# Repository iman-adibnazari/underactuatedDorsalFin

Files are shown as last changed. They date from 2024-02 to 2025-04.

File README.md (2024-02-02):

## Overview
- Proposing an efficient fish robot design where, leveraging the physical properties of the dorsal fin material, only the front part of the fin is motor-driven to initiate wave propagation
- Design a linear quadratic regulator(LQR) and feedforward controller to manage the movement of the fish's fin

## Set up
Install necessary packages listed in requirements.txt:
`$ pip install -r requirements.txt`

## Robot Assembly
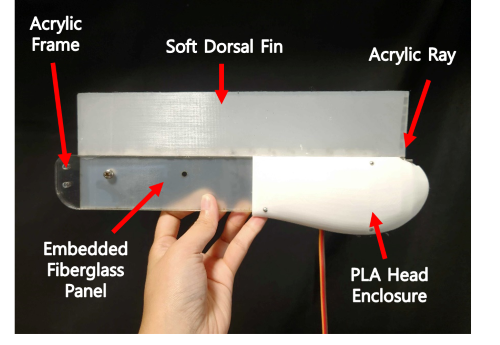
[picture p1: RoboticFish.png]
Schemetic view of robotic fish

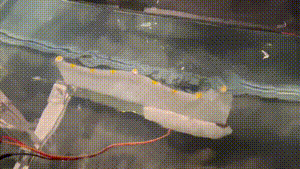
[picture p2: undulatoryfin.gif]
Propulsion of wave through dorsal fin

1. Laser-cut acrylic fin ray, fish body acrylic Frame, Fiberglass Panel
```
cad\Fish\FinRay.SLDPRT
cad\Fish\Body2.SLDPRT
cad\Fish\FIN.SLDPRT
```
2. Build silicone fin using 3D printed mold embedded with FR4 and fin ray 
```
cad\Fin Silicone Mold\Fin_mold_assemble.SLDASM
```
3. 3D printing PLA Head Closure 
```
cad\Fish\Body1_L.SLDPRT
cad\Fish\Body1_R.SLDPRT
```
4. Assemble 
- Mount dowel pin, Savox SW0250MGP motor with left Head Closure
- Attach fin with acrylic body frame
- Combine left head closure and acrylic body frame with fin 

## Control System Modeling
Goal: Aim to control the wave motion of the undulatory dorsal fin of robotic fish
Approach: Employing a frequency-response-based control system modeling method
1. Use top-view video data of the fish's fin, run `src\dataGenProc\multiObjectTracking.py` to calculate each position of the fin over time
2. Run `src\dataGenProc\GenerateBodedata.py` to create Bode plot using the processed video data
3. Run `src\dataGenProc\EstimateTF.m` in MATLAB to estimate Transfer Function from Bode plot, and generate discrete time state-space model
4. Design LQR gain, Kalman filter gain by running `src\dataGenProc\ControllerDesign.m` in MATLAB

## Testing Controller in Robotic Fish
1. Run `src\controlSystem\realTimeTracking.py` to track the tail point of the fin and send it to Arduino
2. Execute `src\controlSystem\discretecontroller\discretecontroller.ino` in Arduino IDE to output motor sine wave frequency

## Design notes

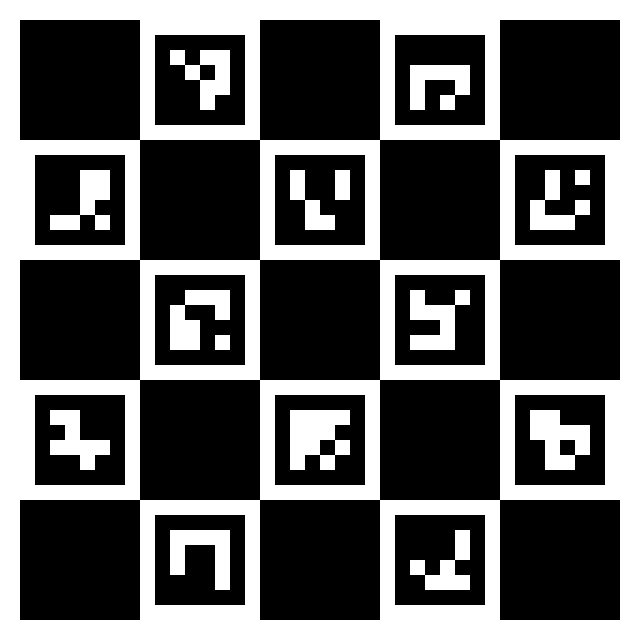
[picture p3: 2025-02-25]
src/python/utils/ChArUco_Marker.png

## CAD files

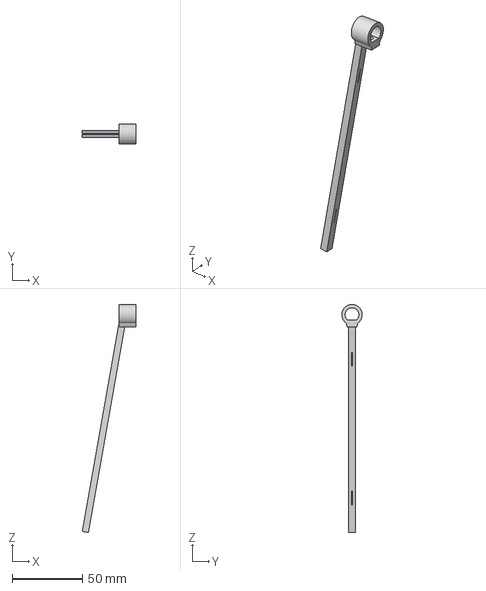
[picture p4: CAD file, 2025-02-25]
cad/CNC/FinRayv184.step
38.0 x 14.5 x 162.1 mm

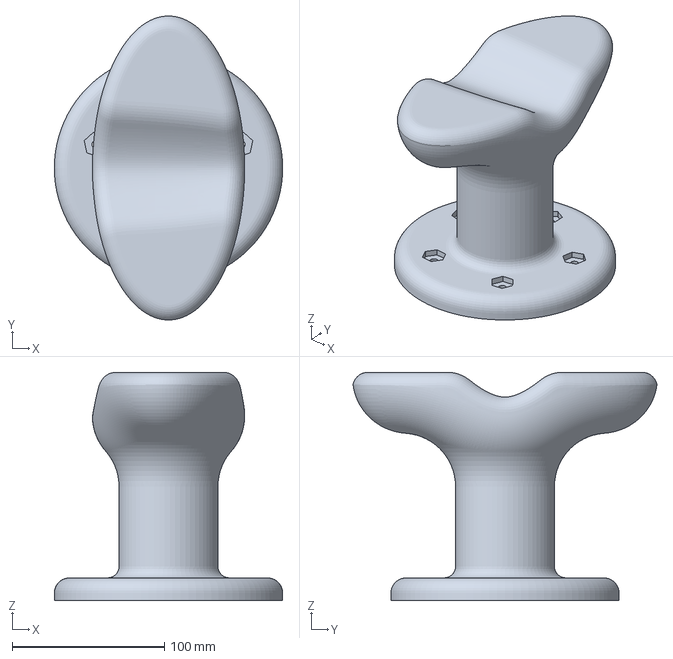
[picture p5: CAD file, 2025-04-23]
cad/fabrication/Bambu/StandPillarRight.3mf
150.0 x 199.6 x 150.0 mm

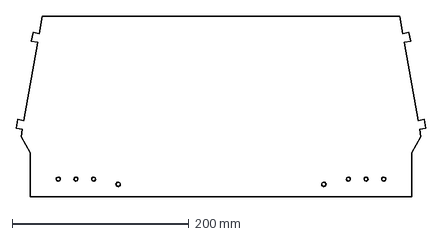
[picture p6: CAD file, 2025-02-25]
cad/fabrication/dxf/Fin_TPU.dxf
463.8 x 204.4 mm

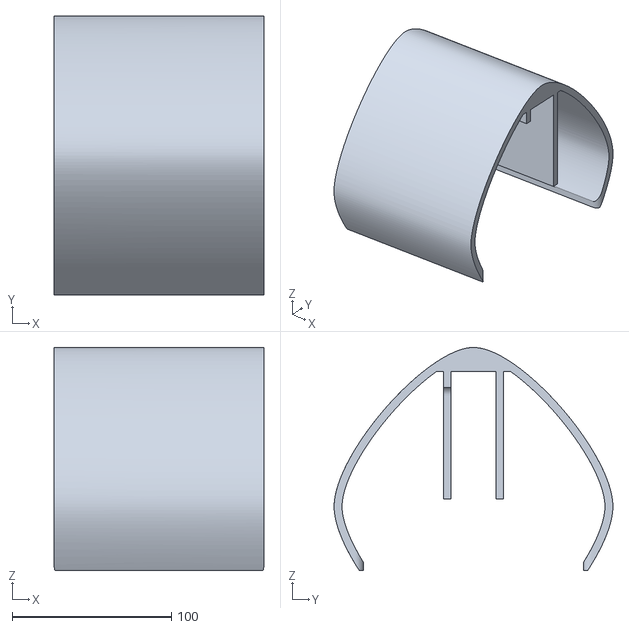
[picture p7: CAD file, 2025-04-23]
cad/fabrication/stl/FrameCover_ExternalFrame_v217.stl
131.8 x 175.0 x 140.0

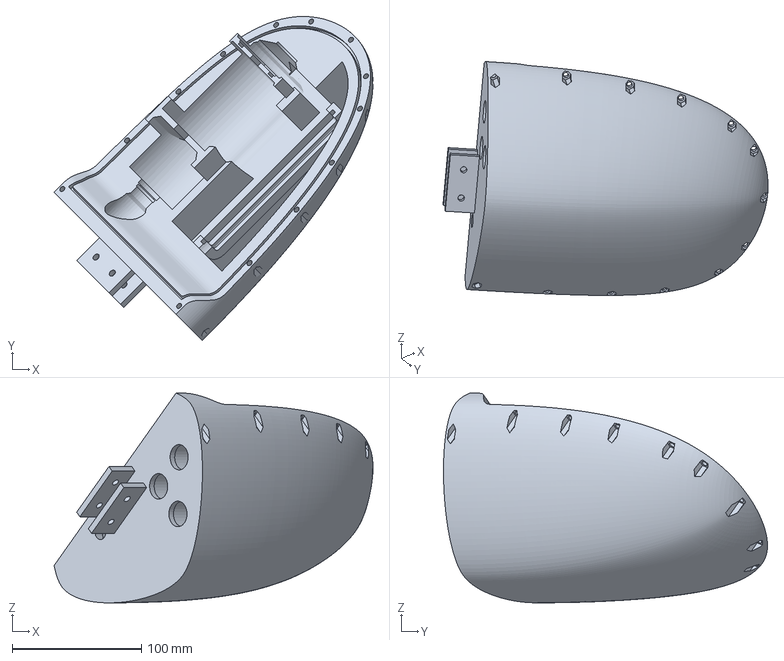
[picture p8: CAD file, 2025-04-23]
cad/fabrication/Bambu/HeadBottom.3mf
246.9 x 250.9 x 162.4 mm

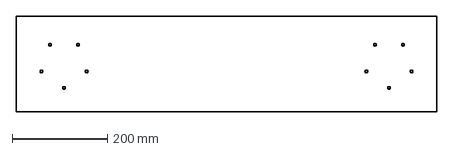
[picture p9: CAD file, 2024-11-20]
cad/fabrication/dxf/StandBase_Acrylic.dxf
882.0 x 200.0 mm

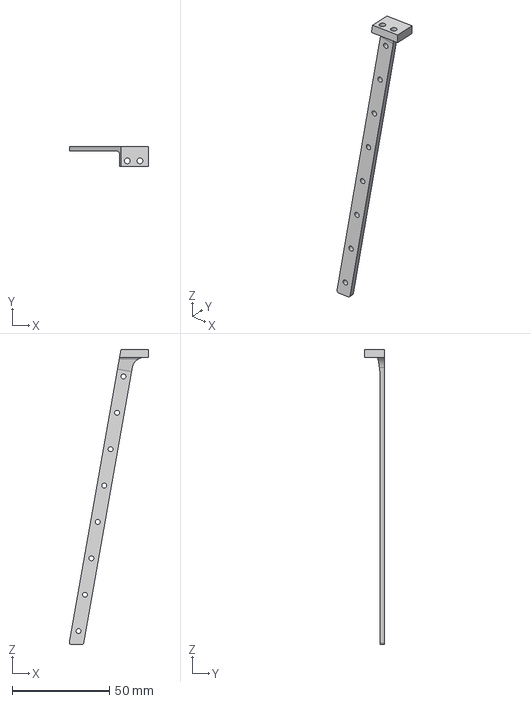
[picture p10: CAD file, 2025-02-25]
cad/fabrication/stepFiles/Finray_v212_Side1.step
40.9 x 10.5 x 151.7 mm

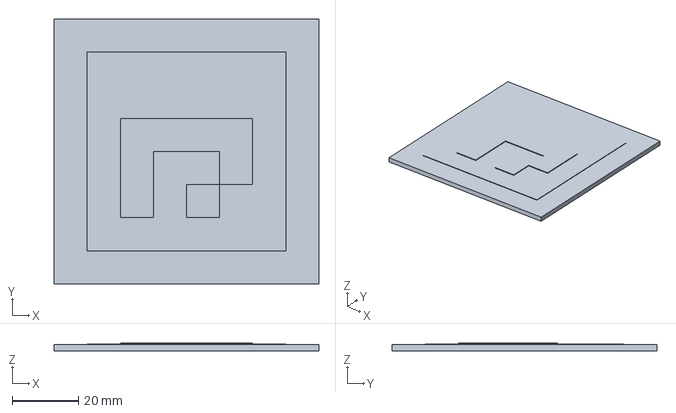
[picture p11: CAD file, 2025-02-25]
cad/fabrication/stl/ArUco_4x4_50_ID1.3mf
80.0 x 80.0 x 2.50 mm

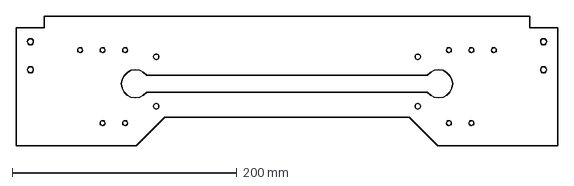
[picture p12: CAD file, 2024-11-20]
cad/fabrication/dxf/BodyFrame_Acrylic.dxf
482.0 x 115.0 mm

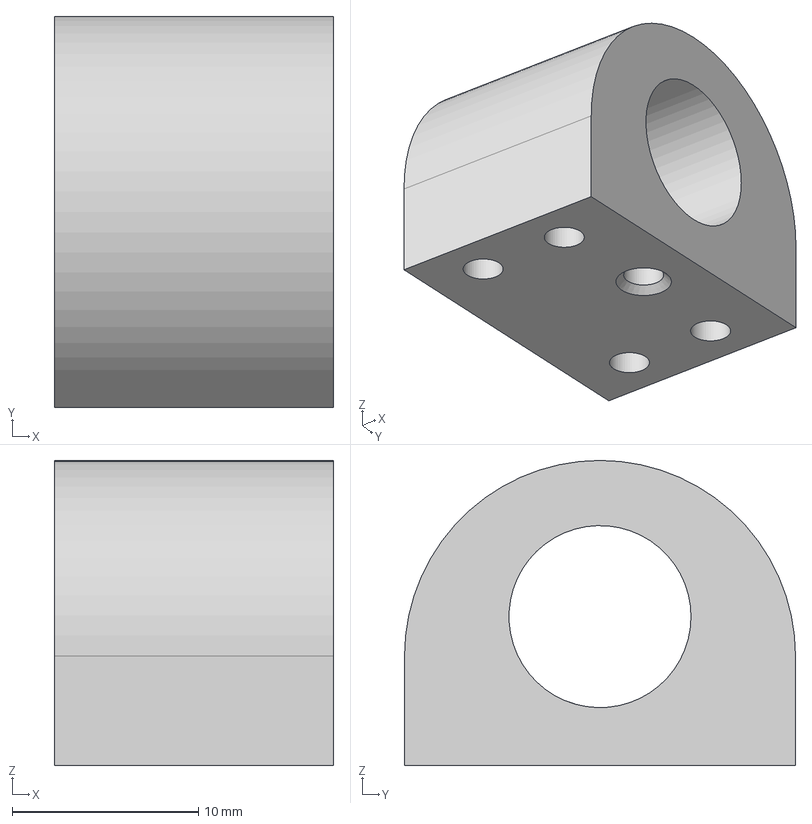
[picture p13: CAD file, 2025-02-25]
cad/fabrication/stepFiles/Finray_v212_ShaftCouple.step
15.0 x 21.0 x 16.4 mm

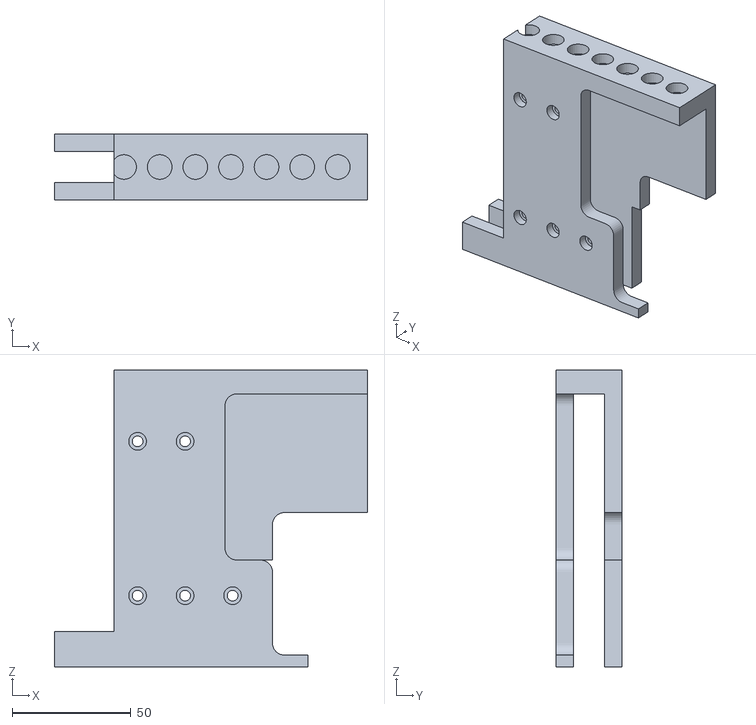
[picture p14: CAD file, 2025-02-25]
cad/fabrication/stl/FrameCover_FrameMount.stl
131.8 x 27.9 x 125.0

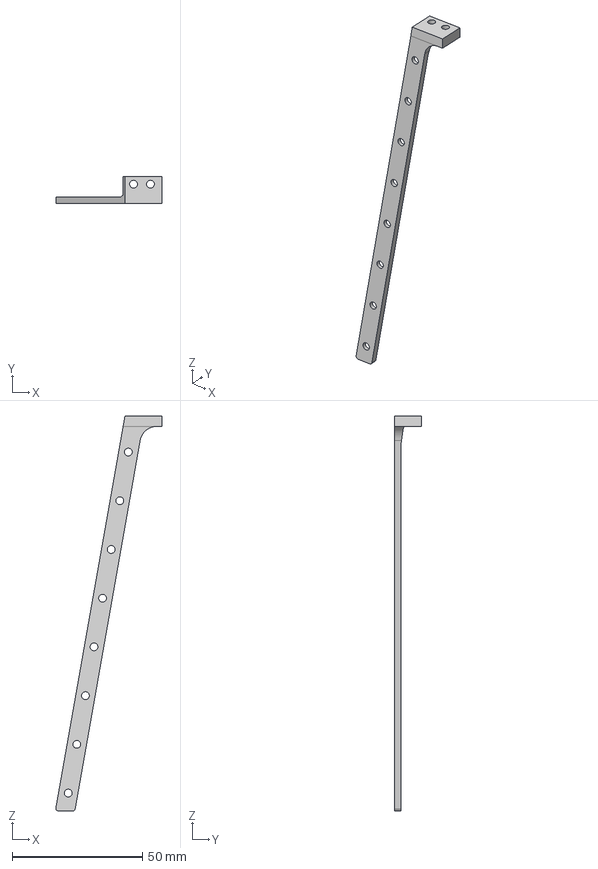
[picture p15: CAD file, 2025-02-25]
cad/fabrication/stepFiles/Finray_v212_Side2.step
40.9 x 10.5 x 151.7 mm

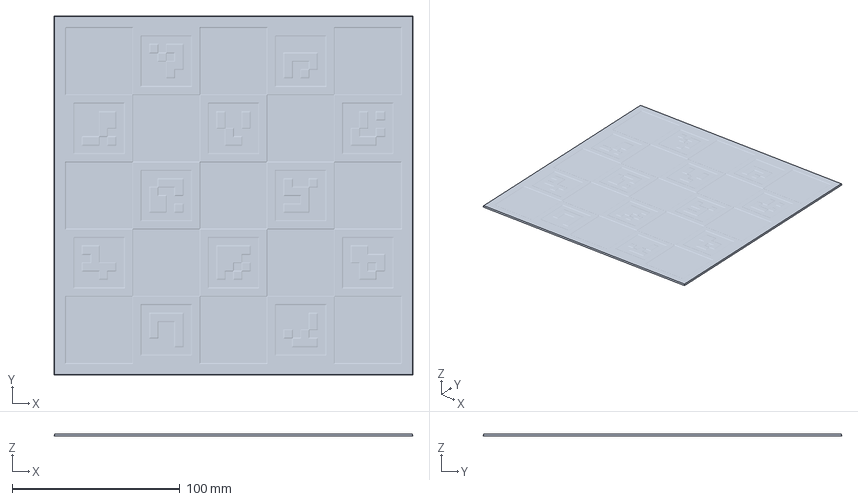
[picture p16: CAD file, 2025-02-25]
cad/fabrication/Bambu/ChArUco_Board_4x4_100_40mmSquares.3mf
213.8 x 213.8 x 1.20 mm

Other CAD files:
cad/fabrication/stepFiles/finRayV193.step
cad/fabrication/Bambu/StandPillars.3mf
cad/fabrication/Bambu/FrameCovers_FrameCoverOnly.3mf
cad/fabrication/stl/FinRay.stl
cad/fabrication/stl/ArUco_4x4_50_ID0.stl
cad/fabrication/Bambu/ArUco_4x4_50_ID0.3mf
cad/fabrication/Bambu/BatteryModule-Covers.3mf
cad/fabrication/Bambu/BatteryModule-ModuleBody.3mf
cad/fabrication/Bambu/BatteryModule-PowerDistBoardHolder.3mf
cad/fabrication/Bambu/ElectronicsBasePlate.3mf
cad/fabrication/Bambu/FinRay.3mf
cad/fabrication/Bambu/FrameCover.3mf
cad/fabrication/Bambu/FrameCovers_FrameMountsOnly.3mf
cad/fabrication/Bambu/HeadTop.3mf
cad/fabrication/Bambu/PowerDistBoardHolder.3mf
cad/fabrication/stepFiles/finRayV190.step
cad/fabrication/stl/ArUco_4x4_50_ID1.stl
cad/fabrication/stl/BatteryModule-BackCover.stl
cad/fabrication/stl/BatteryModule-FrontCover.stl
cad/fabrication/stl/BatteryModule-ModuleBody.stl
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

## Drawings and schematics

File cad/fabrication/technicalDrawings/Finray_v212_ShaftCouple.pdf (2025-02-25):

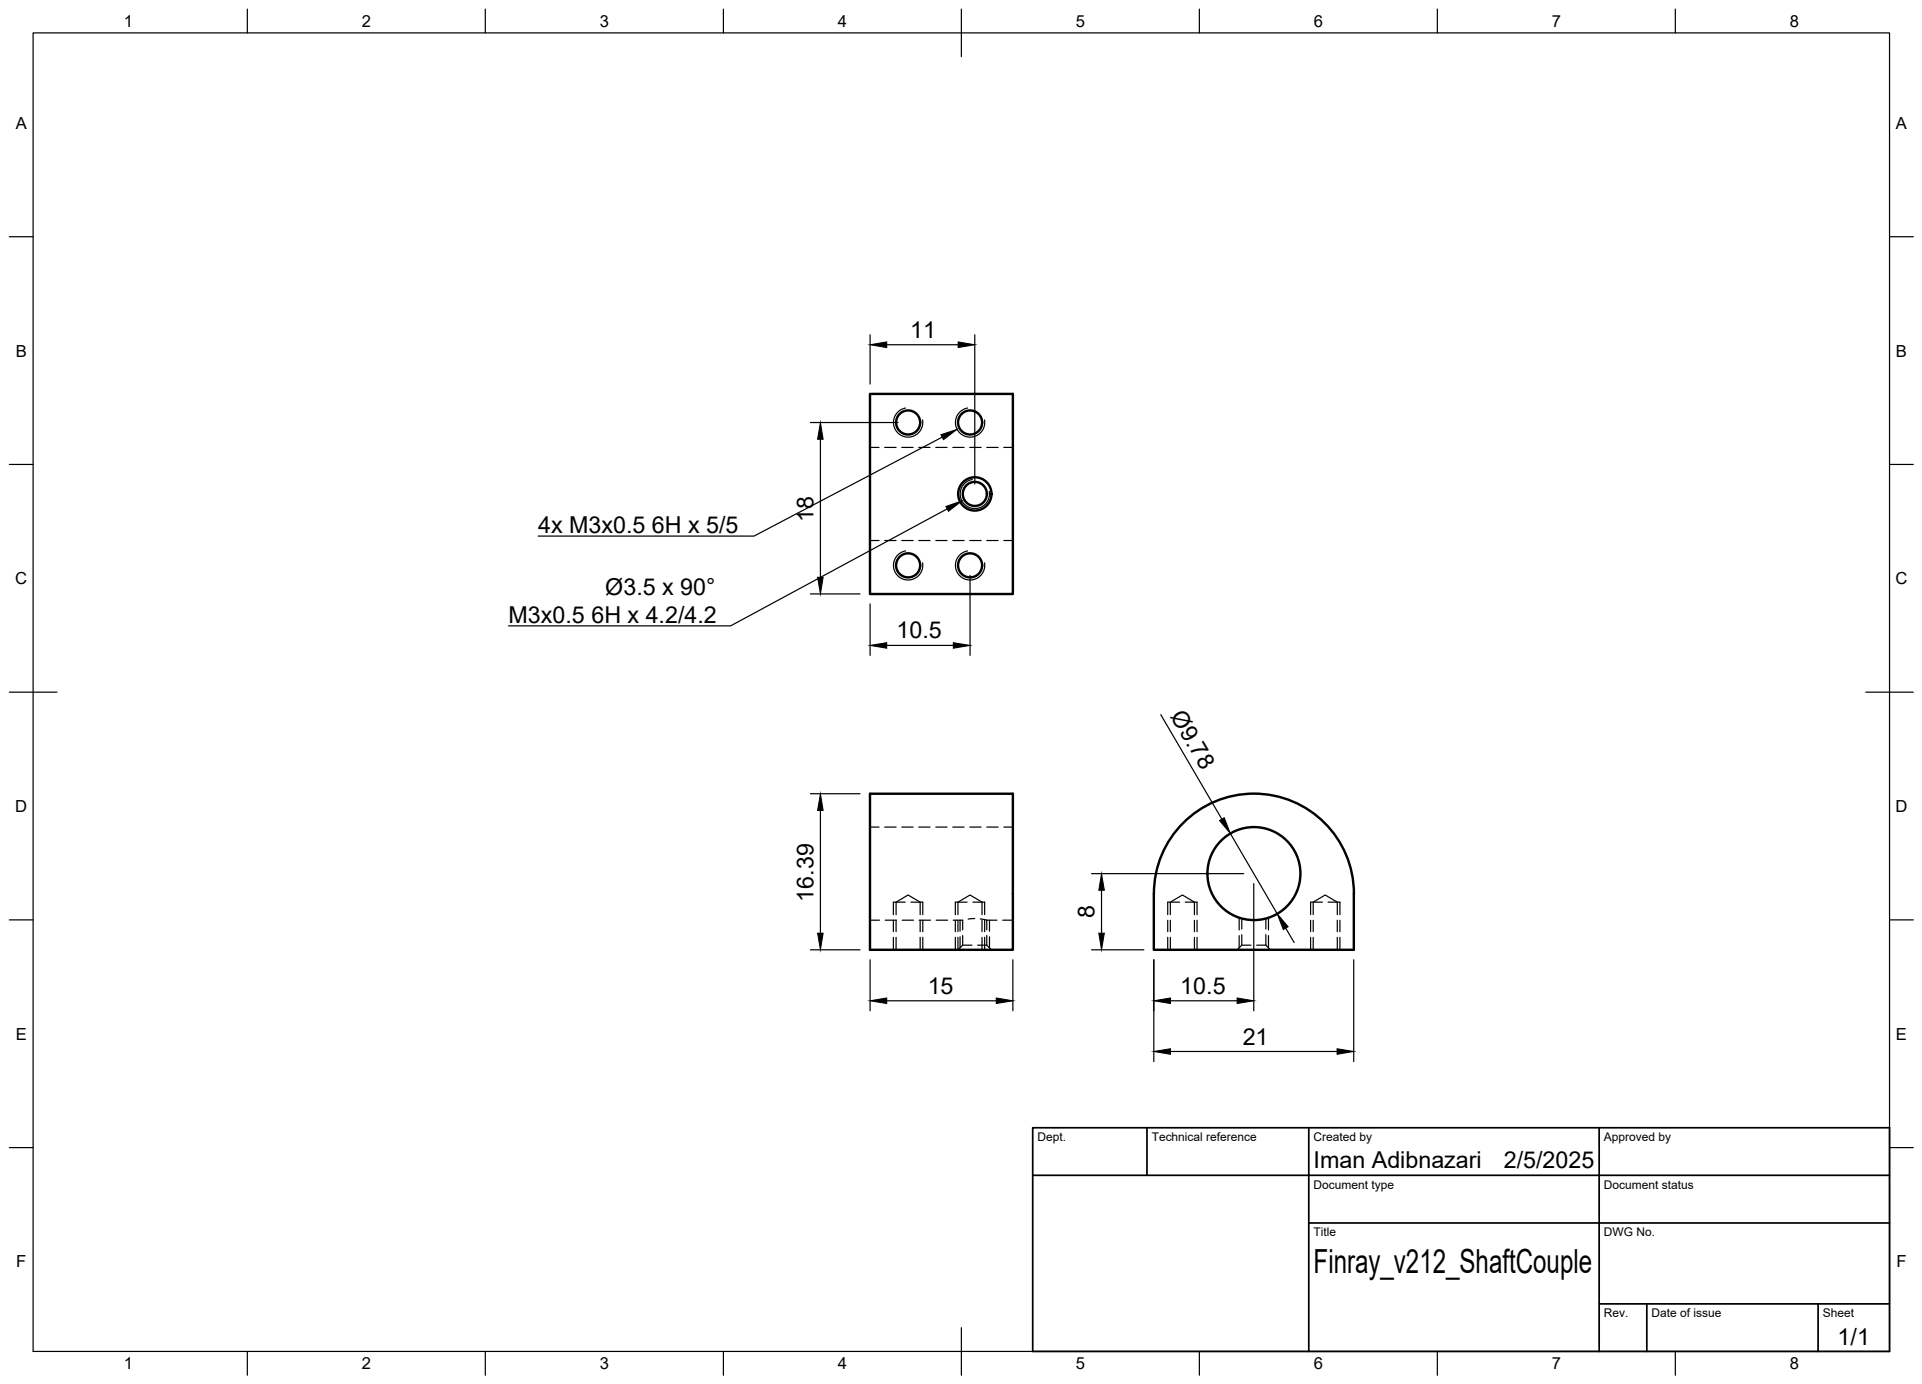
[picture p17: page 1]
Title; DWG No.; Rev.; Date of issue; Sheet; Iman Adibnazari 16.39

Dept. | Technical reference | Created by 2/5/2025 | Approved by

Document type | Document status

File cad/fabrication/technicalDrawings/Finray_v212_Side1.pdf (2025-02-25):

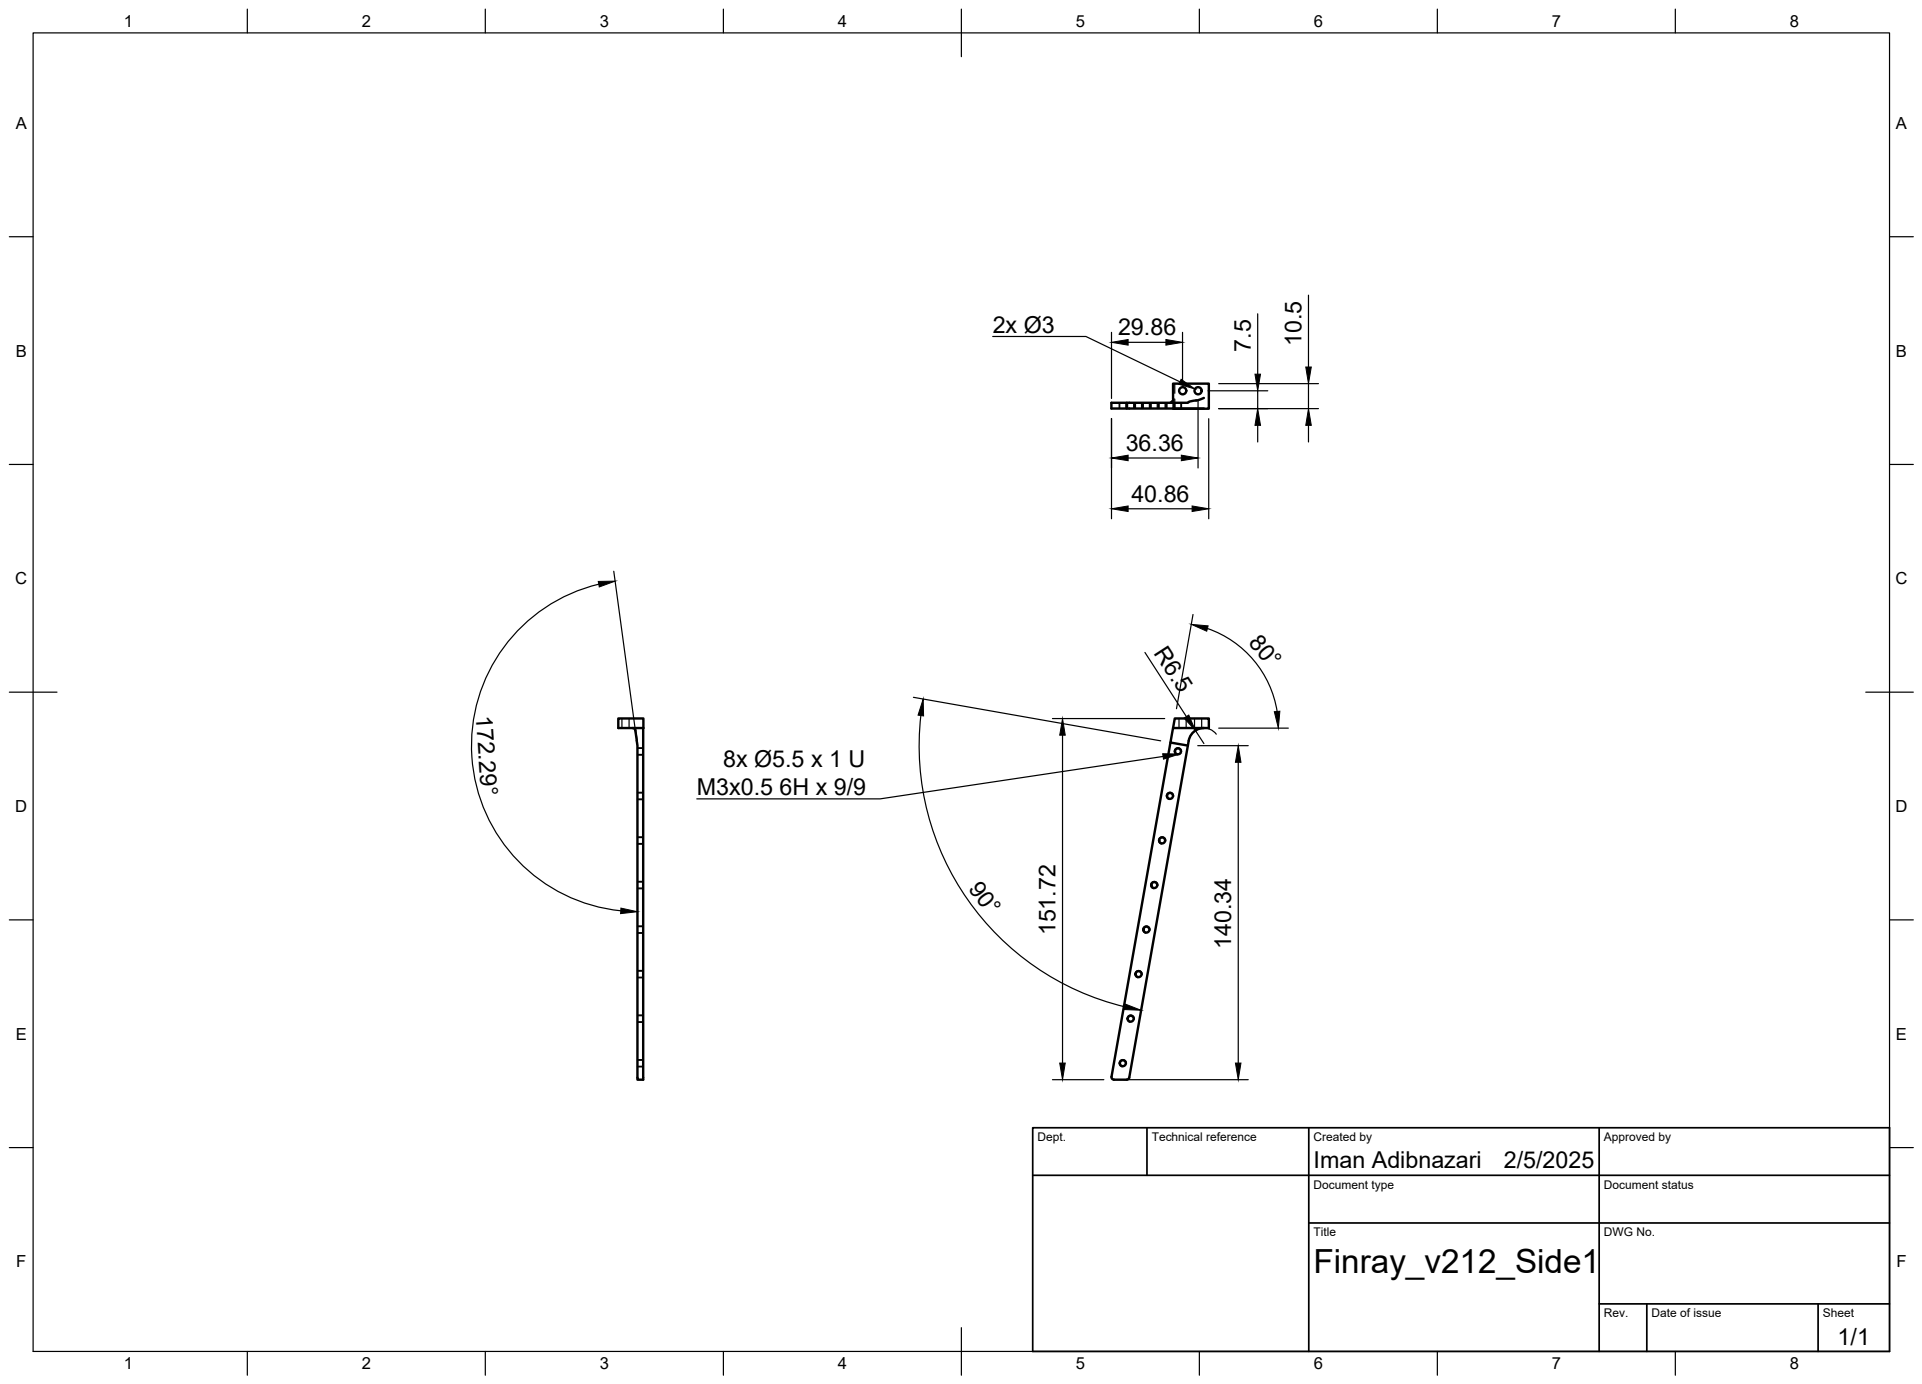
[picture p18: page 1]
Title; DWG No.; Rev.; Date of issue; Sheet; Iman Adibnazari 10.5 151.72 2x Ø3

Dept. | Technical reference | Created by 2/5/2025 | Approved by

Document type | Document status

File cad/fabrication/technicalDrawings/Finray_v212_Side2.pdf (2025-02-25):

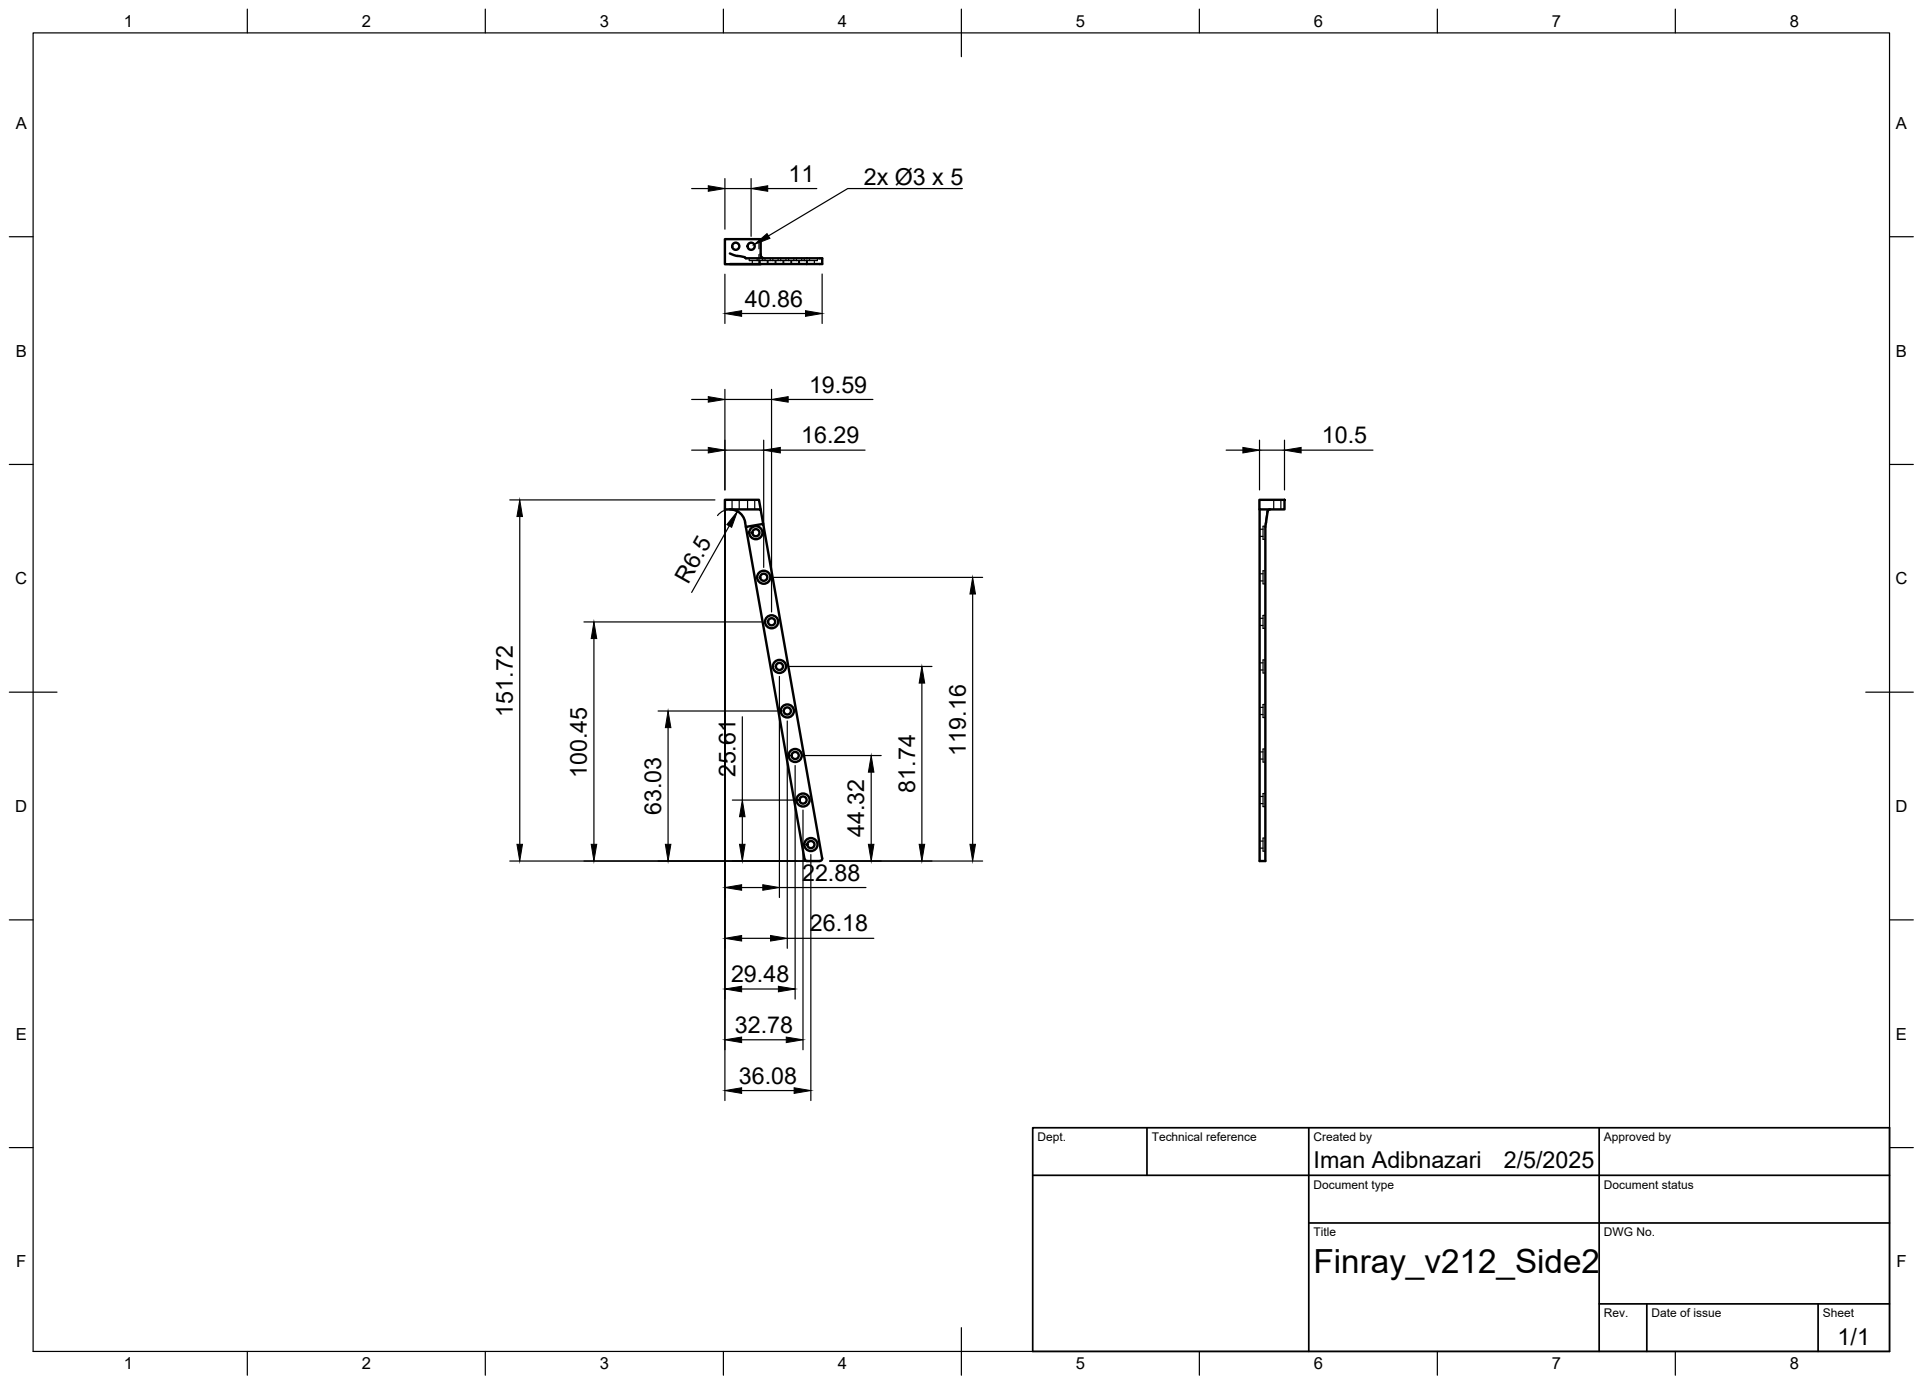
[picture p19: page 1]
Title; DWG No.; Rev.; Date of issue; Sheet

Dept. | Technical reference | Created by Iman Adibnazari 2/5/2025 | Approved by

Document type | Document status

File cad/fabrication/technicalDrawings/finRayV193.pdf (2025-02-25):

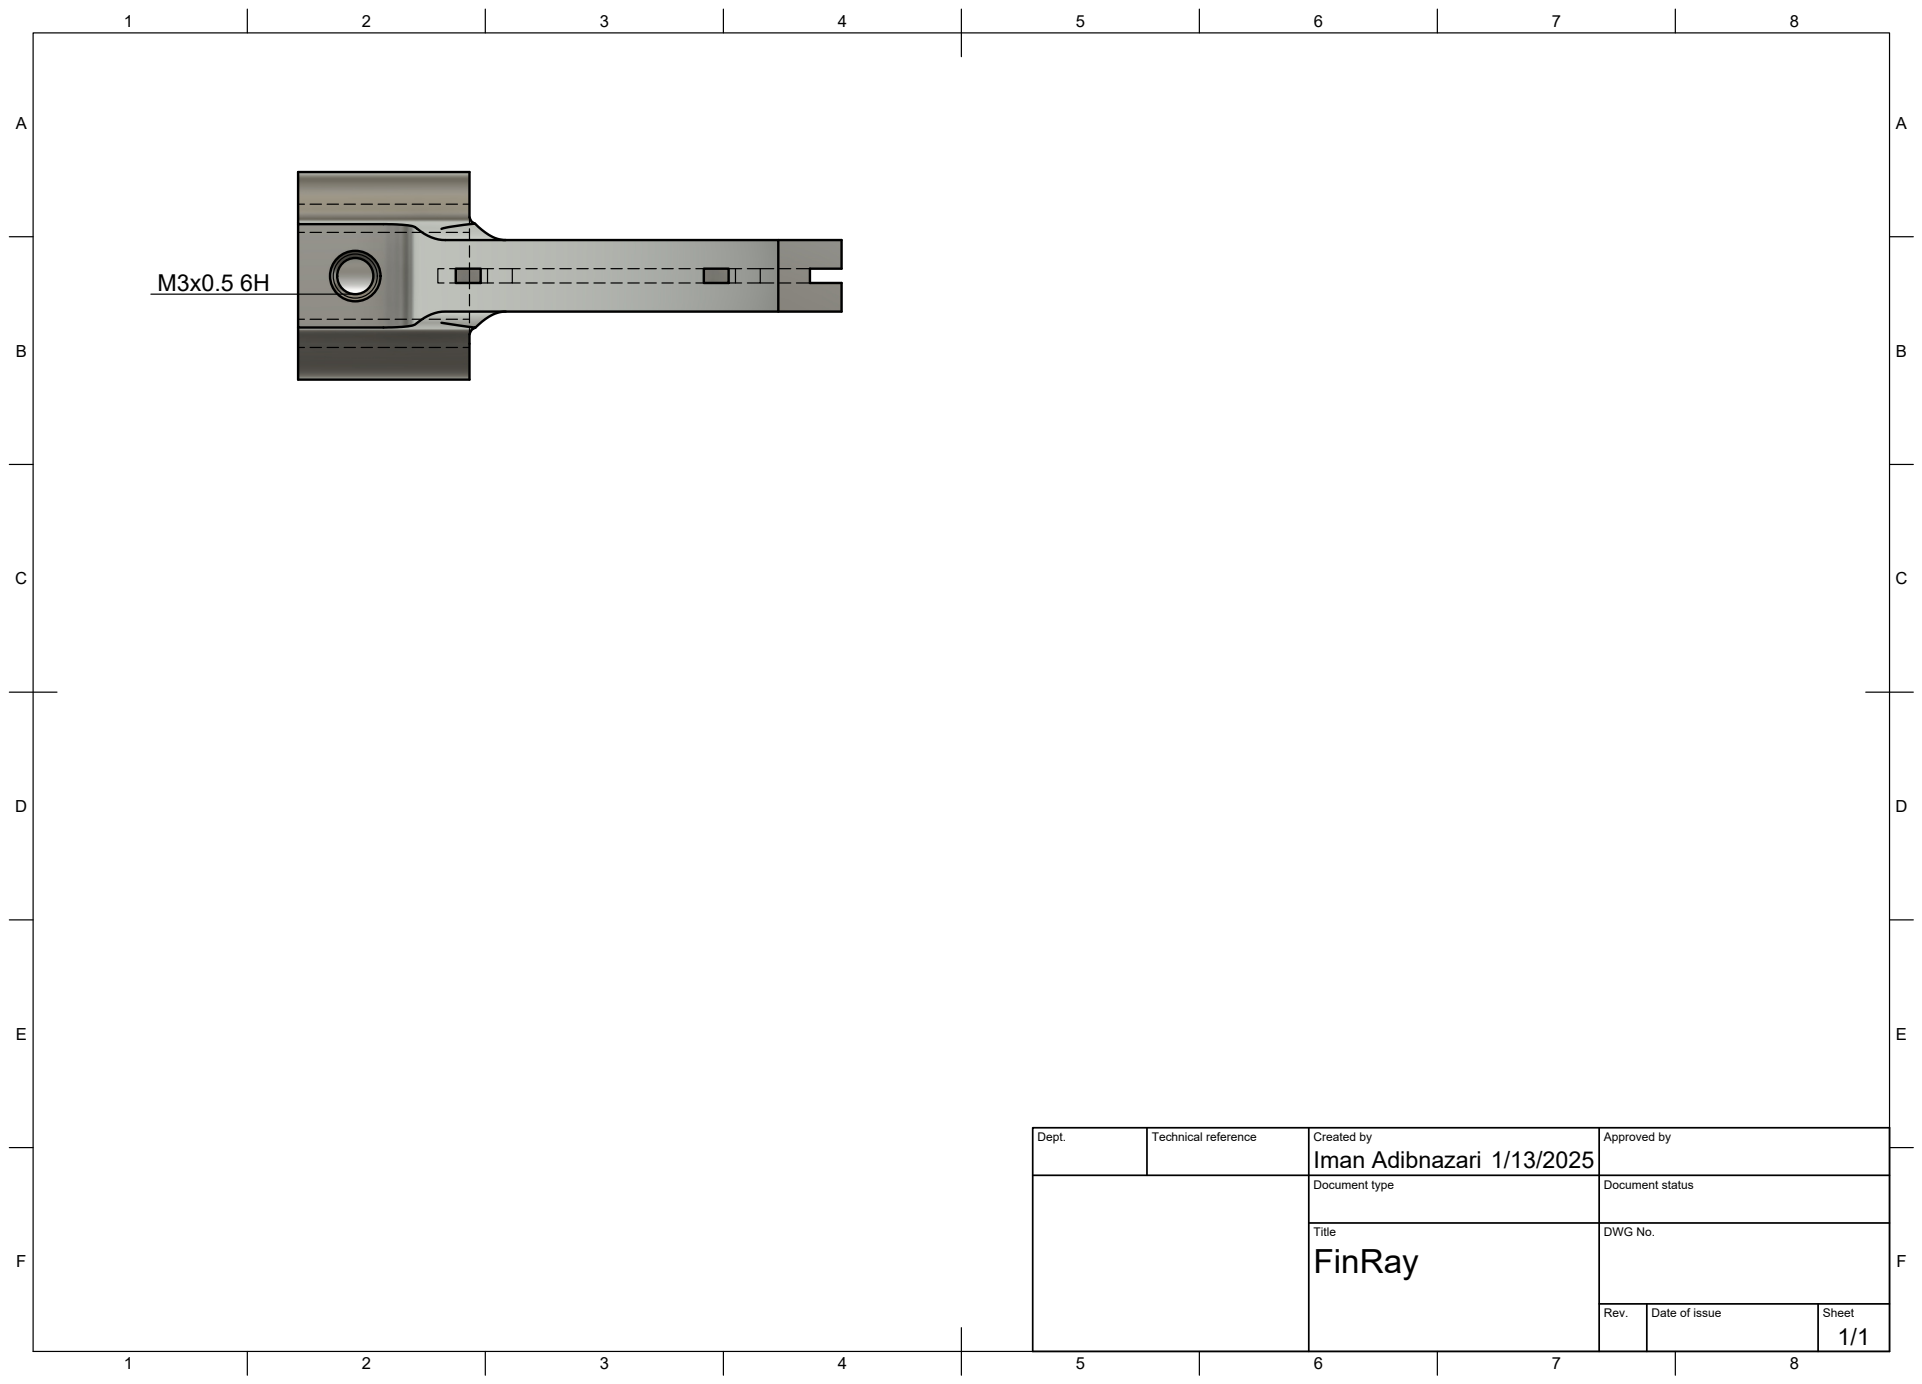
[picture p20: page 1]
Title; DWG No.; Rev.; Date of issue; Sheet

Dept. | Technical reference | Created by Iman Adibnazari 1/13/2025 | Approved by

Document type | Document status

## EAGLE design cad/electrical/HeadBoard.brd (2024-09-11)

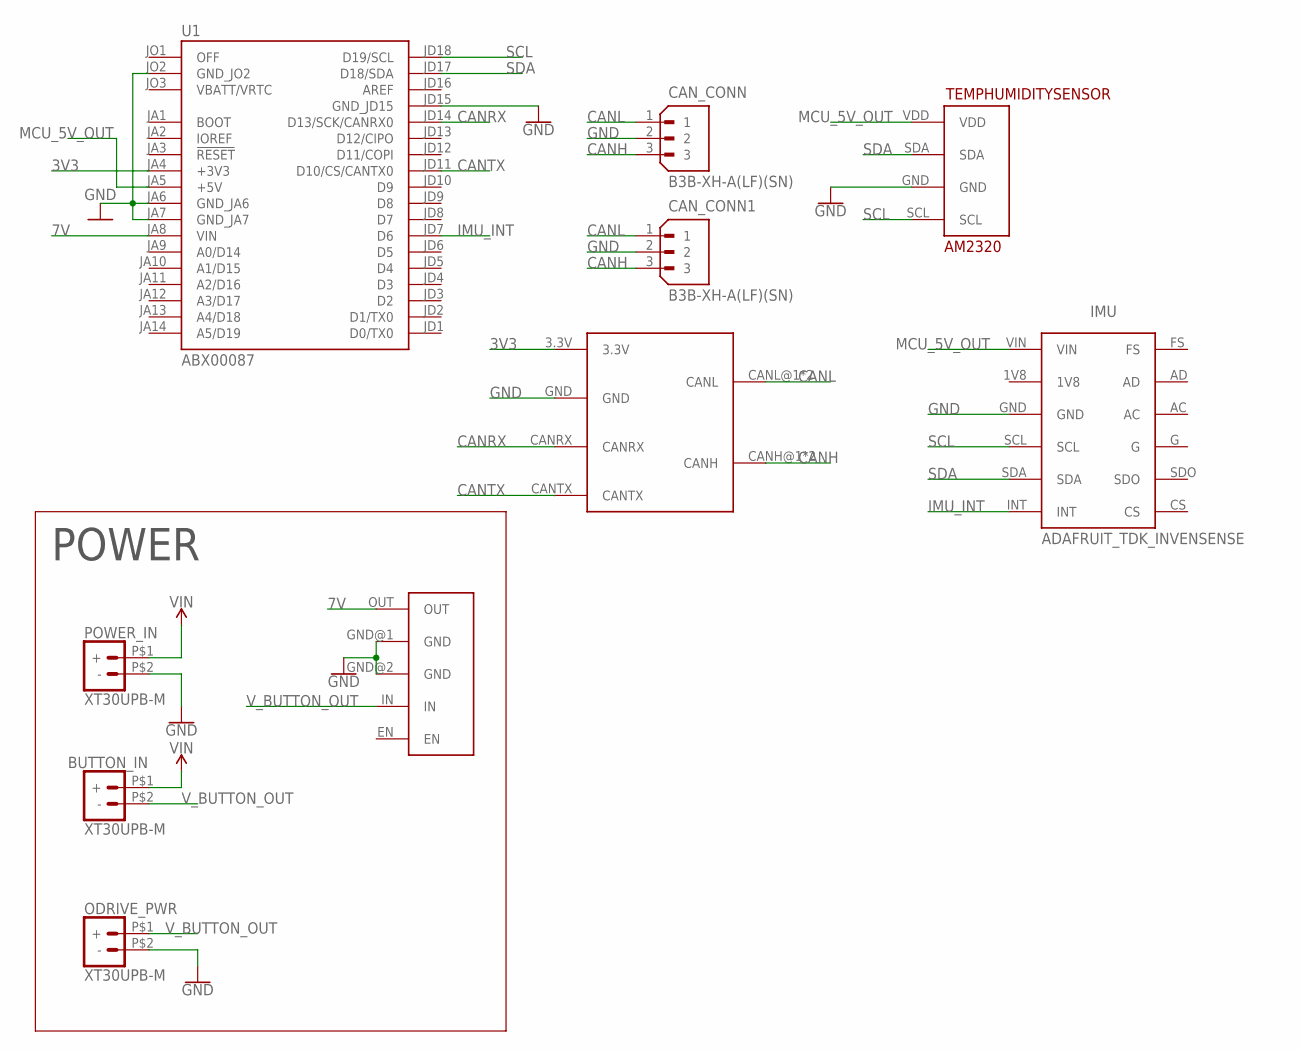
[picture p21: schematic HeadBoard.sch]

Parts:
BUTTON_IN: XT30UPB-M
CAN_CONN, CAN_CONN1: B3B-XH-A(LF)(SN); JST_B3B-XH-A(LF)(SN)
IMU: ADAFRUIT_TDK_INVENSENSE
ODRIVE_PWR: XT30UPB-M
POWER_IN: XT30UPB-M
TEMPHUMIDITYSENSOR: AM2320
U1: ABX00087; MODULE_ABX00087
U$1: D36V28F7; D36V28F5
U$2: WAVESHARE_SN65HVD230

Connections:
3V3: U1.JA4 (+3V3), U$2.3.3V
7V: U1.JA8 (VIN), U$1.OUT
CANH: CAN_CONN.3, CAN_CONN1.3, U$2.CANH@1 (CANH), U$2.CANH@2 (CANH)
CANL: CAN_CONN.1, CAN_CONN1.1, U$2.CANL@1 (CANL), U$2.CANL@2 (CANL)
CANRX: U1.JD14 (D13/SCK/CANRX0), U$2.CANRX
CANTX: U1.JD11 (D10/CS/CANTX0), U$2.CANTX
GND: CAN_CONN.2, CAN_CONN1.2, IMU.GND, ODRIVE_PWR.P$2 (-), POWER_IN.P$2 (-), TEMPHUMIDITYSENSOR.GND, U1.JA6 (GND_JA6), U1.JA7 (GND_JA7), U1.JD15 (GND_JD15), U1.JO2 (GND_JO2), U$1.GND@1 (GND), U$1.GND@2 (GND), U$2.GND
IMU_INT: IMU.INT, U1.JD7 (D6)
MCU_5V_OUT: IMU.VIN, TEMPHUMIDITYSENSOR.VDD, U1.JA5 (+5V)
SCL: IMU.SCL, TEMPHUMIDITYSENSOR.SCL, U1.JD18 (D19/SCL)
SDA: IMU.SDA, TEMPHUMIDITYSENSOR.SDA, U1.JD17 (D18/SDA)
VBATT/VRTC: U1.JO3 (VBATT/VRTC)
VIN: BUTTON_IN.P$1 (+), POWER_IN.P$1 (+)
V_BUTTON_OUT: BUTTON_IN.P$2 (-), ODRIVE_PWR.P$1 (+), U$1.IN

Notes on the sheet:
POWER

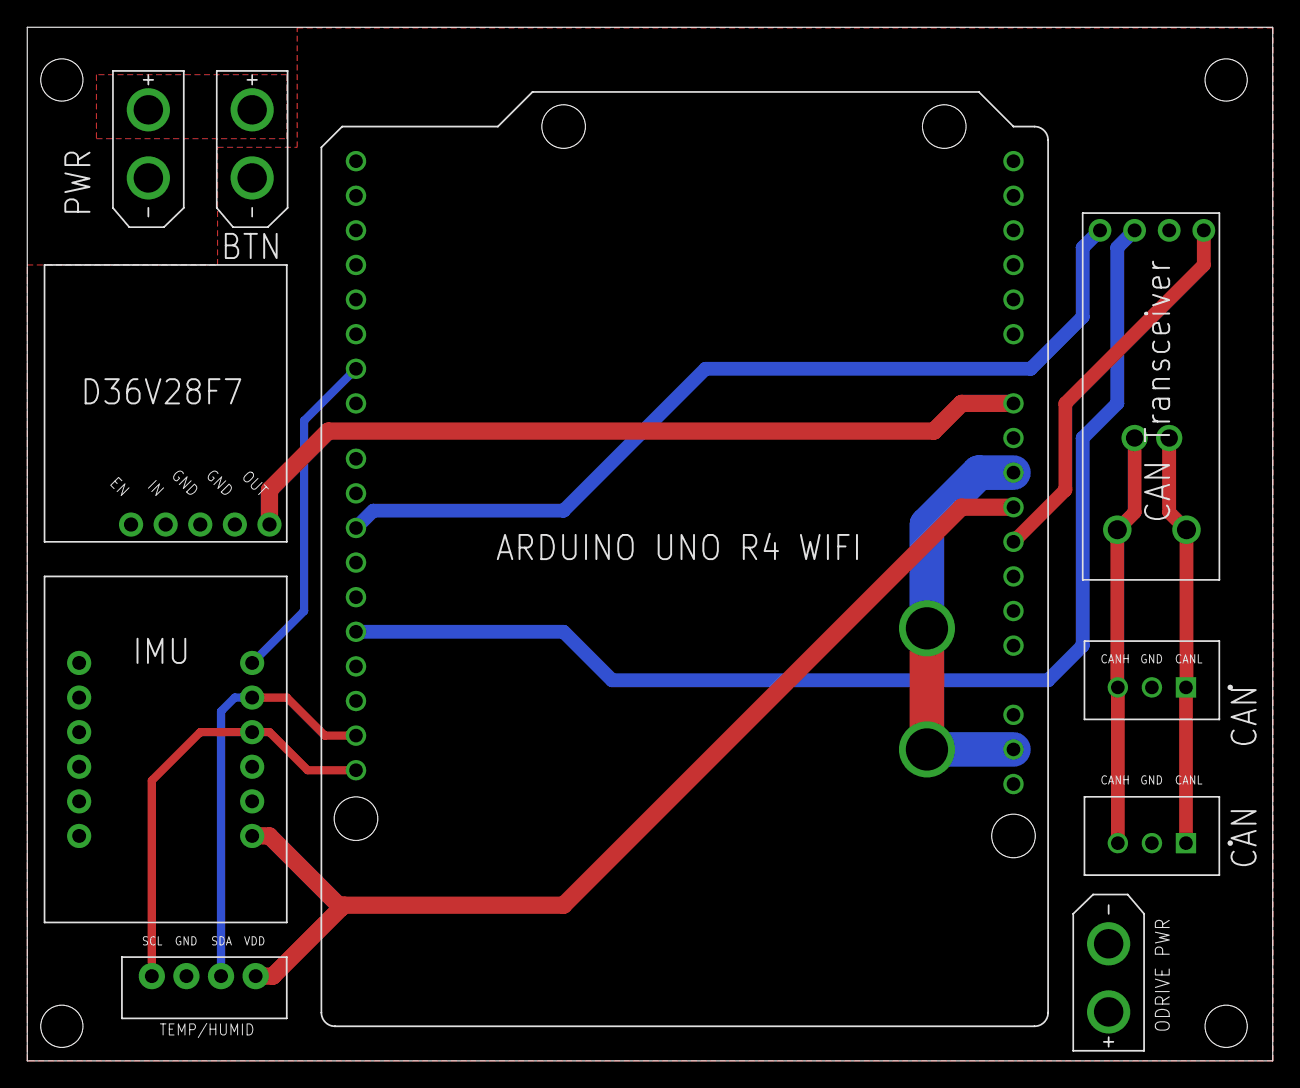
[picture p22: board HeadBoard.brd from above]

Board: 2 copper layers, 91.4 x 75.9 mm, 10 parts (0 on the bottom side), 13 nets.

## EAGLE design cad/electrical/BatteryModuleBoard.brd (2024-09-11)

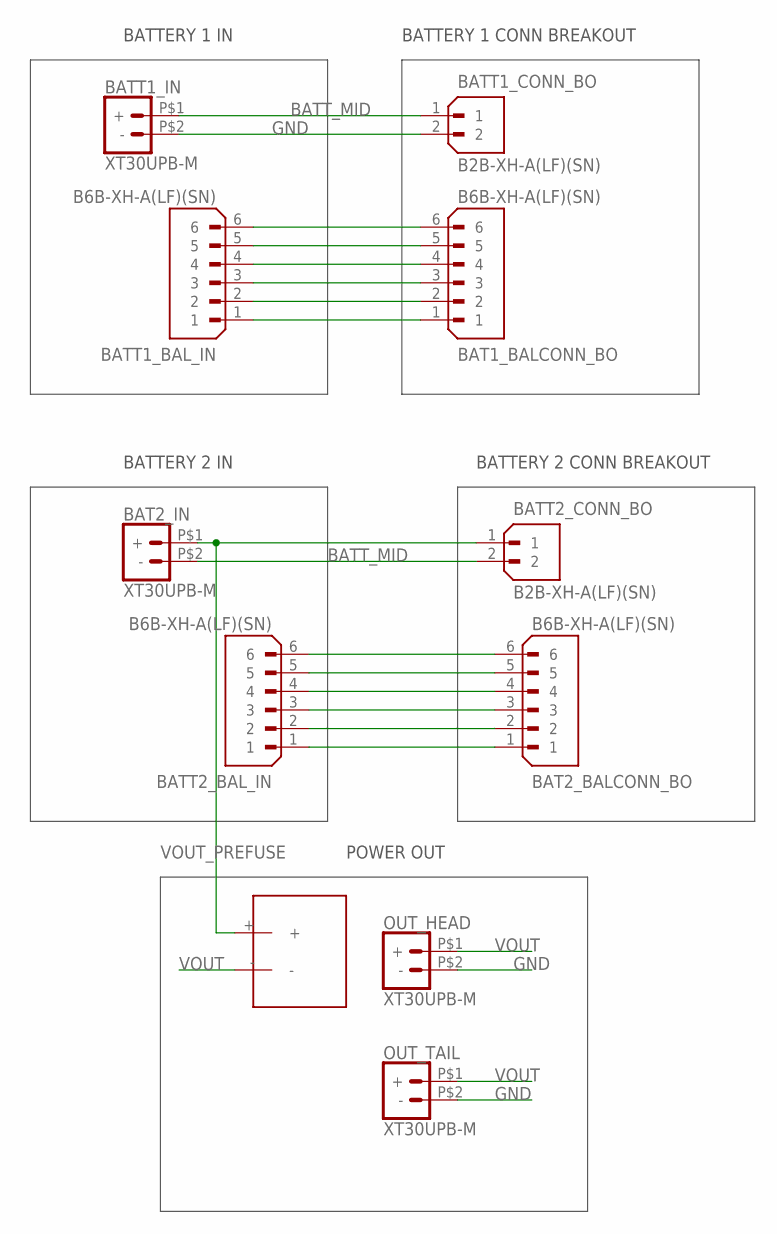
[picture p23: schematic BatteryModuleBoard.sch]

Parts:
BAT1_BALCONN_BO, BAT2_BALCONN_BO: B6B-XH-A(LF)(SN); JST_B6B-XH-A(LF)(SN)
BAT2_IN: XT30UPB-M
BATT1_BAL_IN, BATT2_BAL_IN: B6B-XH-A(LF)(SN); JST_B6B-XH-A(LF)(SN)
BATT1_CONN_BO, BATT2_CONN_BO: B2B-XH-A(LF)(SN); JST_B2B-XH-A(LF)(SN)
BATT1_IN: XT30UPB-M
FUSE: SETSAFE_C1_FUSE
OUT_HEAD: XT30UPB-M
OUT_TAIL: XT30UPB-M

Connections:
BATT_MID: BAT2_IN.P$2 (-), BATT1_CONN_BO.1, BATT1_IN.P$1 (+), BATT2_CONN_BO.2
GND: BATT1_CONN_BO.2, BATT1_IN.P$2 (-), OUT_HEAD.P$2 (-), OUT_TAIL.P$2 (-)
unnamed: BAT1_BALCONN_BO.6, BATT1_BAL_IN.6
unnamed: BAT1_BALCONN_BO.5, BATT1_BAL_IN.5
unnamed: BAT1_BALCONN_BO.4, BATT1_BAL_IN.4
unnamed: BAT1_BALCONN_BO.3, BATT1_BAL_IN.3
unnamed: BAT1_BALCONN_BO.2, BATT1_BAL_IN.2
unnamed: BAT1_BALCONN_BO.1, BATT1_BAL_IN.1
unnamed: BAT2_BALCONN_BO.6, BATT2_BAL_IN.6
unnamed: BAT2_BALCONN_BO.5, BATT2_BAL_IN.5
unnamed: BAT2_BALCONN_BO.4, BATT2_BAL_IN.4
unnamed: BAT2_BALCONN_BO.3, BATT2_BAL_IN.3
unnamed: BAT2_BALCONN_BO.2, BATT2_BAL_IN.2
unnamed: BAT2_BALCONN_BO.1, BATT2_BAL_IN.1
VOUT: FUSE.-, OUT_HEAD.P$1 (+), OUT_TAIL.P$1 (+)
VOUT_PREFUSE: BAT2_IN.P$1 (+), BATT2_CONN_BO.1, FUSE.+

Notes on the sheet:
BATTERY 1 IN
BATTERY 2 IN
BATTERY 1 CONN BREAKOUT
BATTERY 2 CONN BREAKOUT
POWER OUT

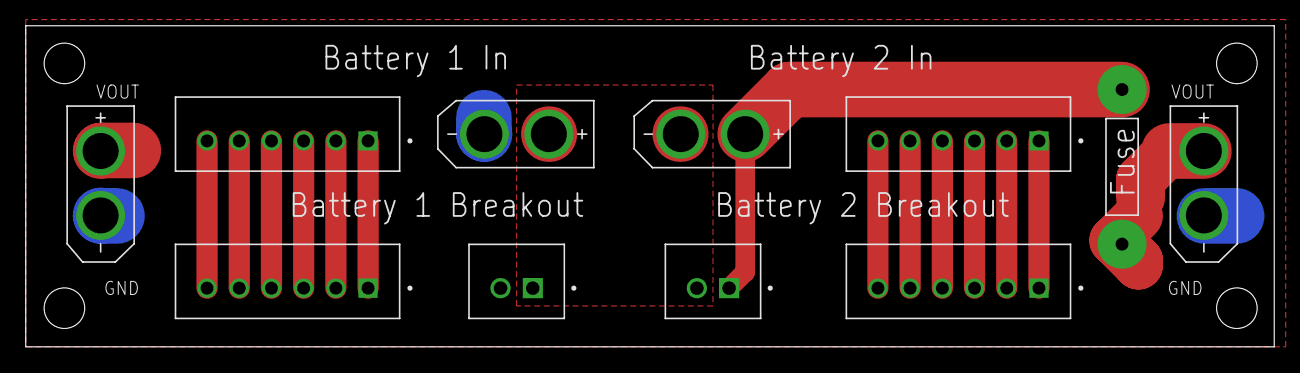
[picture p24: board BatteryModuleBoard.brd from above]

Board: 2 copper layers, 96.9 x 24.9 mm, 11 parts (0 on the bottom side), 16 nets.

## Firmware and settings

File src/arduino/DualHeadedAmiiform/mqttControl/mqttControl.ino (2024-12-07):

#include <Arduino.h>
#include "ODriveCAN.h"

#include <ArduinoMqttClient.h>
#include "WiFiS3.h"
#include "arduino_secrets.h"
#define PI 3.1415926535897932384626433832795


///////please enter your sensitive data in the Secret tab/arduino_secrets.h
char ssid[] = SECRET_SSID;        // your network SSID (name)
char pass[] = SECRET_PASS;    // your network password (use for WPA, or use as key for WEP)

WiFiClient wifiClient;
MqttClient mqttClient(wifiClient);


const char broker[] = "192.168.0.114"; // PUT IN BROKER IP HERE
int        port     = 1883;
const char topic[]  = "robot/start";
const char topic2[]  = "robot/stop";
const char topic3[]  = "robot/gait";

//set interval for sending messages (milliseconds)
const long interval = 8000;
unsigned long previousMillis = 0;

int count = 0;

// Initialize gait parameters
float A_f = 0; 
float f = 0;
float b_f = 0;
float A_b = 0;
float b_b = 0;
float phi = 0;

// Initialize variables to hold finray angles and velocities
float theta_f = 0;
float theta_b = 0;
float thetad_f = 0;
float thetad_b = 0;

// Initialize flags and variables for finite state machine that define if robot should run or not
bool isRunning = false;
bool runFlag = false;
float startDelay = 0; 
float stopDelay = 0;

long startDelayTime = 0;
long stopDelayTime = 0;

// time variable for running gaits 
long startedRunningTime = 0;



// Initialize buffer for holding received MQTT messages

char MQTTReceiveBuffer[50]; // buffer is 50 bytes


/* ------------- CAN SETUP  -------------  */
// TODO: Finish setting up CAN for both odrives using the dualOdriveTest exmample code
// CAN bus baudrate. Make sure this matches for every device on the bus
#define CAN_BAUDRATE 250000

// ODrive node_id for odrv0
#define ODRV0_NODE_ID 0
#define ODRV1_NODE_ID 1

// Uncomment below the line that corresponds to your hardware.
// See also "Board-specific settings" to adapt the details for your hardware setup.

// #define IS_TEENSY_BUILTIN // Teensy boards with built-in CAN interface (e.g. Teensy 4.1). See below to select which interface to use.
#define IS_ARDUINO_BUILTIN // Arduino boards with built-in CAN interface (e.g. Arduino Uno R4 Minima)
// #define IS_MCP2515 // Any board with external MCP2515 based extension module. See below to configure the module.


/* Board-specific includes ---------------------------------------------------*/


// See https://github.com/arduino/ArduinoCore-API/blob/master/api/HardwareCAN.h
// and https://github.com/arduino/ArduinoCore-renesas/tree/main/libraries/Arduino_CAN

#include <Arduino_CAN.h>
#include <ODriveHardwareCAN.hpp>





/* Board-specific settings ---------------------------------------------------*/



/* Arduinos with built-in CAN */


HardwareCAN& can_intf = CAN;

bool setupCan() {
  return can_intf.begin((CanBitRate)CAN_BAUDRATE);
}



/* Example sketch ------------------------------------------------------------*/

// Instantiate ODrive objects
ODriveCAN odrv0(wrap_can_intf(can_intf), ODRV0_NODE_ID); // Standard CAN message ID
ODriveCAN odrv1(wrap_can_intf(can_intf), ODRV1_NODE_ID); // Standard CAN message ID
ODriveCAN* odrives[] = {&odrv0,&odrv1}; // Make sure all ODriveCAN instances are accounted for here

struct ODriveUserData {
  Heartbeat_msg_t last_heartbeat;
  bool received_heartbeat = false;
  Get_Encoder_Estimates_msg_t last_feedback;
  bool received_feedback = false;
};

// Keep some application-specific user data for every ODrive.
ODriveUserData odrv0_user_data;
ODriveUserData odrv1_user_data;

// Called every time a Heartbeat message arrives from the ODrive
void onHeartbeat(Heartbeat_msg_t& msg, void* user_data) {
  ODriveUserData* odrv_user_data = static_cast<ODriveUserData*>(user_data);
  odrv_user_data->last_heartbeat = msg;
  odrv_user_data->received_heartbeat = true;
}

// Called every time a feedback message arrives from the ODrive
void onFeedback(Get_Encoder_Estimates_msg_t& msg, void* user_data) {
  ODriveUserData* odrv_user_data = static_cast<ODriveUserData*>(user_data);
  odrv_user_data->last_feedback = msg;
  odrv_user_data->received_feedback = true;
}

// Called for every message that arrives on the CAN bus
void onCanMessage(const CanMsg& msg) {
  for (auto odrive: odrives) {
    onReceive(msg, *odrive);
  }
}

void setup() {
  //Initialize serial and wait for port to open:
  delay(3000);
  Serial.begin(115200);
  while (!Serial) {
    ; // wait for serial port to connect. Needed for native USB port only
  }
  Serial.println("Got here");
    // delay(10000);

  /* --- CAN SETUP --- */
  Serial.println("Starting ODriveCAN");

  // Register callbacks for the heartbeat and encoder feedback messages
  odrv0.onFeedback(onFeedback, &odrv0_user_data);
  odrv0.onStatus(onHeartbeat, &odrv0_user_data);  
  odrv1.onFeedback(onFeedback, &odrv1_user_data);
  odrv1.onStatus(onHeartbeat, &odrv1_user_data);

  // Configure and initialize the CAN bus interface. This function depends on
  // your hardware and the CAN stack that you're using.
  if (!setupCan()) {
    Serial.println("CAN failed to initialize: reset required");
    while (true); // spin indefinitely
  }

  Serial.println("Waiting for ODrive 0...");
  while (!odrv0_user_data.received_heartbeat) {
    pumpEvents(can_intf);
    delay(100);
  }
  Serial.println("Waiting for ODrive 1...");
  while (!odrv1_user_data.received_heartbeat) {
    pumpEvents(can_intf);
    delay(100);
  }

  Serial.println("found ODrives!");

  // request bus voltage and current (1sec timeout)
  Serial.println("attempting to read bus voltage and current");
  Get_Bus_Voltage_Current_msg_t vbus;
  if (!odrv0.request(vbus, 1)) {
    Serial.println("vbus request failed!");
    while (true); // spin indefinitely
  }

  Serial.print("DC voltage [V]: ");
  Serial.println(vbus.Bus_Voltage);
  Serial.print("DC current [A]: ");
  Serial.println(vbus.Bus_Current);

  Serial.println("Enabling closed loop control for ODrive 0...");
  while (odrv0_user_data.last_heartbeat.Axis_State != ODriveAxisState::AXIS_STATE_CLOSED_LOOP_CONTROL) {
    odrv0.clearErrors();
    delay(1);
    odrv0.setState(ODriveAxisState::AXIS_STATE_CLOSED_LOOP_CONTROL);
    // Pump events for 150ms. This delay is needed for two reasons;
    // 1. If there is an error condition, such as missing DC power, the ODrive might
    //    briefly attempt to enter CLOSED_LOOP_CONTROL state, so we can't rely
    //    on the first heartbeat response, so we want to receive at least two
    //    heartbeats (100ms default interval).
    // 2. If the bus is congested, the setState command won't get through
    //    immediately but can be delayed.
    for (int i = 0; i < 15; ++i) {
      delay(10);
      pumpEvents(can_intf);
    }
  }
  Serial.println("Enabling closed loop control for ODrive 1...");
  while (odrv1_user_data.last_heartbeat.Axis_State != ODriveAxisState::AXIS_STATE_CLOSED_LOOP_CONTROL) {
    odrv1.clearErrors();
    delay(1);
    odrv1.setState(ODriveAxisState::AXIS_STATE_CLOSED_LOOP_CONTROL);
    // Pump events for 150ms. This delay is needed for two reasons;
    // 1. If there is an error condition, such as missing DC power, the ODrive might
    //    briefly attempt to enter CLOSED_LOOP_CONTROL state, so we can't rely
    //    on the first heartbeat response, so we want to receive at least two
    //    heartbeats (100ms default interval).
    // 2. If the bus is congested, the setState command won't get through
    //    immediately but can be delayed.
    for (int i = 0; i < 15; ++i) {
      delay(10);
      pumpEvents(can_intf);
    }
  }

  Serial.println("ODrives running!");

  /* --- MQTT SETUP --- */
  
  // attempt to connect to Wifi network:
  Serial.print("Attempting to connect to WPA SSID: ");
  Serial.println(ssid);
  while (WiFi.begin(ssid, pass) != WL_CONNECTED) {
    // failed, retry
    Serial.print(".");
    delay(5000);
  }



  Serial.println("You're connected to the network");
  Serial.println();

  Serial.print("Attempting to connect to the MQTT broker: ");
  Serial.println(broker);
  unsigned int reconnectTime=3000;
  unsigned int mqttAttempts = 0;
  while (!mqttClient.connect(broker, port)) {
    mqttAttempts++;
    Serial.print("MQTT connection attempt ");
    Serial.print(mqttAttempts);
    Serial.print(" failed! Error code = ");
    Serial.println(mqttClient.connectError());
    delay(reconnectTime);
    reconnectTime+=1000;
    
    

    // while (1);
  }

  Serial.println("You're connected to the MQTT broker!");
  Serial.println();

  // set the message receive callback
  mqttClient.onMessage(onMqttMessage);

  Serial.print("Subscribing to topic: ");
  Serial.println(topic);
  Serial.println();

  // subscribe to a topic
  mqttClient.subscribe(topic);
  mqttClient.subscribe(topic2);
  mqttClient.subscribe(topic3);

  // topics can be unsubscribed using:
  // mqttClient.unsubscribe(topic);

  Serial.print("Topic: ");
  Serial.println(topic);
  Serial.print("Topic: ");
  Serial.println(topic2);
  Serial.print("Topic: ");
  Serial.println(topic3);

}


void loop() {
  // call poll() regularly to allow the library to send MQTT keep alive which
  // avoids being disconnected by the broker
  mqttClient.poll();
  // Check if start/stop state needs to be switched
  stepFSM();
  pumpEvents(can_intf); // This is required on some platforms to handle incoming feedback CAN messages

  // Calculate finray angle
  if (isRunning==true){
    float time = float(millis()-startedRunningTime)/1000.0; // seconds
    // compute finray angles from gait parameters
    theta_f = A_f*sin(2*PI*f*time) + b_f;
    theta_b = A_b*sin(2*PI*f*time + phi)+ b_b;

    thetad_f = A_f*2*PI*f*cos(2*PI*f*time);
    thetad_b = A_b*2*PI*f*cos(2*PI*f*time+phi);

    // Serial.println("RUNNING");
  //   float SINE_PERIOD = 0.2f; // Period of the position command sine wave in seconds

  // float t = 0.001 * millis();
  
  // float phase = t * (TWO_PI / SINE_PERIOD);
  // float amplitude = 0.05;

  // odrv0.setPosition(
  //   amplitude*sin(phase), // position
  //   amplitude*cos(phase) * (TWO_PI / SINE_PERIOD) // velocity feedforward (optional)
  // );
  // delay(2);
  // odrv1.setPosition(
  //   amplitude*sin(phase), // position
  //   amplitude*cos(phase) * (TWO_PI / SINE_PERIOD) // velocity feedforward (optional)
  // );
  // delay(2);

  }
  else{
  // float SINE_PERIOD = 0.2f; // Period of the position command sine wave in seconds

  // float t = 0.001 * millis();
  
  // float phase = t * (TWO_PI / SINE_PERIOD);
  // float amplitude = 0.01;

  // odrv0.setPosition(
  //   amplitude*sin(phase), // position
  //   amplitude*cos(phase) * (TWO_PI / SINE_PERIOD) // velocity feedforward (optional)
  // );
  // delay(2);
  // odrv1.setPosition(
  //   amplitude*sin(phase), // position
  //   amplitude*cos(phase) * (TWO_PI / SINE_PERIOD) // velocity feedforward (optional)
  // );
  // delay(2);

    // set finray angles to 0
    // Serial.println("STOPPED");
    theta_f = 0;
    theta_b = 0;
    thetad_f = 0;
    thetad_b = 0;
    
  }
  // // TODO: Send joint angles over CAN bus
  // // Serial.print("theta_f: ");
  // Serial.print(theta_f);
  // // Serial.print(", theta_b: ");
  // Serial.print("\t");
  // Serial.print(theta_b);
  // // Serial.print(", thetad_f: ");
  // Serial.print("\t");
  // Serial.print(thetad_f);
  // // Serial.print(", thetad_b: ");
  // Serial.print("\t");
  // Serial.println(thetad_b);
    
  odrv0.setPosition(
    theta_f, // position
    thetad_f // velocity feedforward (optional)
  );
  delay(2);
  odrv1.setPosition(
    theta_b, // position
    thetad_b // velocity feedforward (optional)
  );
  delay(2);

  // TODO: Sensing/sending data back 

    // print position and velocity for Serial Plotter
  if (odrv0_user_data.received_feedback) {
    Get_Encoder_Estimates_msg_t feedback = odrv0_user_data.last_feedback;
    odrv0_user_data.received_feedback = false;
    Serial.print("odrv0-pos:");
    Serial.print(feedback.Pos_Estimate);
    Serial.print(",");
    Serial.print("odrv0-vel:");
    Serial.println(feedback.Vel_Estimate);
  }
  if (odrv1_user_data.received_feedback) {
    Get_Encoder_Estimates_msg_t feedback = odrv1_user_data.last_feedback;
    odrv1_user_data.received_feedback = false;
    Serial.print("odrv1-pos:");
    Serial.print(feedback.Pos_Estimate);
    Serial.print(",");
    Serial.print("odrv1-vel:");
    Serial.println(feedback.Vel_Estimate);
  }




}


void onMqttMessage(int messageSize) {
  // Depending on the message topic, run associated handler
  String messageTopic = mqttClient.messageTopic();
  if (messageTopic == "robot/start"){
    startTopicHandler();
  }
  else if (messageTopic == "robot/stop"){
    stopTopicHandler();
  }
  else if (messageTopic == "robot/gait"){
    gaitTopicHandler();
  }
}

void startTopicHandler(){
  // Serial.println("Got a start topic here");
  // Dump whole message into buffer
  int buffIndex = 0;
  while (mqttClient.available()) {
    MQTTReceiveBuffer[buffIndex] = (char)mqttClient.read();
    buffIndex++;
  }
  // Parse value using strtok
  char* value_str = strtok(MQTTReceiveBuffer, ","); // read in comma delimited token 
  // Check if we got a valid token
  if (value_str != NULL) {
    // Convert string to float
    startDelay = atof(value_str);
  } else {
    // Handle error - not enough values in message
    startDelay = 0.0;  // or some error value
  }
  // Set variables for finite state machine controlling start/stop state
  runFlag = true; // Set runflag to true
  startDelayTime = millis() + long(startDelay*1000.0);
  // Serial.print("Current time: ");
  // Serial.print(millis());
  // Serial.print(" Starting in ");
  // Serial.print(startDelay);
  // Serial.print("seconds at: ");
  // Serial.println(startDelayTime);



}
void stopTopicHandler(){
  // Serial.println("Got a stop topic here");
  // Dump whole message into buffer
  int buffIndex = 0;
  while (mqttClient.available()) {
    MQTTReceiveBuffer[buffIndex] = (char)mqttClient.read();
    buffIndex++;
  }

  // Parse value using strtok
  char* value_str = strtok(MQTTReceiveBuffer, ","); // read in comma delimited token 
  // Check if we got a valid token
  if (value_str != NULL) {
    // Convert string to float
    stopDelay = atof(value_str);
  } else {
    // Handle error - not enough values in message
    stopDelay = 0.0; // or some error value
  }

    // Set variables for finite state machine controlling start/stop state
  runFlag = false; // Set runflag to false
  stopDelayTime = millis() + long(stopDelay*1000.0);
  // Serial.print("Current time: ");
  // Serial.print(millis());
  // Serial.print(" Stopping in ");
  // Serial.print(stopDelay);
  // Serial.print("seconds at: ");
  // Serial.println(stopDelayTime);
}
void gaitTopicHandler(){
  // Serial.println("Got a gait topic here");
  // Dump whole message into buffer
  int buffIndex = 0;
  while (mqttClient.available()) {
    MQTTReceiveBuffer[buffIndex] = (char)mqttClient.read();
    buffIndex++;
  }
  parseMessage(MQTTReceiveBuffer); // read in the gait parameters from the message

}

void parseMessage(char* message) {
  float values[6];  // Adjust size based on your needs
  char* ptr = message;
  
  // Parse each value using strtok()
  for (int i = 0; i < 6; i++) { // there are 6 parameter values that are being read in from the message
    char* value_str = strtok(i == 0 ? ptr : NULL, ","); // read in comma delimited token 
    
    // Check if we got a valid token
    if (value_str != NULL) {
      // Convert string to float
      values[i] = atof(value_str);
    } else {
      // Handle error - not enough values in message
      values[i] = 0.0;  // or some error value
    }
  }
  // Assign values
  A_f = values[0]; 
  f = values[1]; 
  b_f = values[2]; 
  A_b = values[3]; 
  b_b = values[4]; 
  phi = values[5]; 

  // // print off all values

  // Serial.print("A_f: ");
  // Serial.print(A_f);
  // Serial.print(" f: ");
  // Serial.print(f);
  // Serial.print(" b_f: ");
  // Serial.print(b_f);
  // Serial.print(" A_b: ");
  // Serial.print(A_b);
  // Serial.print(" b_b: ");
  // Serial.print(b_b);
  // Serial.print(" phi: ");
  // Serial.println(phi);
}

void stepFSM(){
  long time = millis();
  // check state switching conditions
  if (isRunning&&(!runFlag)&&(time-stopDelayTime>=0)){ // if currently running, commanded to stop, and if delay period has passed, then switch to stop state
    isRunning = false;
  } 
  if ((!isRunning)&&runFlag&&(time-startDelayTime>=0)){ // if currently stopped, commanded to run, and if delay period has passed, then switch to running state
    isRunning = true;
    startedRunningTime= millis();
  } 

}

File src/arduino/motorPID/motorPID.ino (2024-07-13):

#include <Encoder.h>

#define ENCA 2 // YELLOW from polulu encoder
#define ENCB 3 // WHITE from polulu encoder

#define IN2 7 //in2 from driver // pins to control direction
#define IN1 6 //in1 from driver // pins to control direction
#define pwmpin 5 //pwm to control speed

#define stepsPerRot  970.0
#define degPerStep 360.0/stepsPerRot

#define kp 20.0
#define kd 0.1
#define ki 0.05

#define pwmMax 255
#define pwmMin 0


float time = 0;
float prevTime = 0;
float error = 0;
float prevError = 0;
float cumError = 0;
float controlSignal = 0;
float ref = 0;

Encoder myEnc(2, 3);

long oldPosition  = -999;

float getAngle(Encoder enc){
  return enc.read()*degPerStep;
}

long startTime = 0;


void setSpeed(int controlSignal, int dirPin1, int dirPin2, int pwmPin){
  // Serial.print("control signal: ");
  // Serial.println(controlSignal);
  int pwmSignal = max(min(pwmMax,abs(controlSignal)),pwmMin);
  bool direction = (controlSignal >=0);

  // if speed is positive spin forward
  if(direction){
    // Set direction forward
  digitalWrite(IN1,HIGH);
  digitalWrite(IN2,LOW);
  analogWrite(pwmpin,pwmSignal);
  }
  else{
        // Set direction backward
  digitalWrite(IN1,LOW);
  digitalWrite(IN2,HIGH);
  analogWrite(pwmpin,pwmSignal);

  }


}

void computeControlSignal(){
  prevTime = time;
  time = millis()/1000.0;
  float dt = time-prevTime;
  prevError = error;
  error = ref - getAngle(myEnc);
  
  cumError += error*dt;

  controlSignal = kp*error + ki*cumError + kd*(error-prevError)/dt;
  

}


void setup() {
  pinMode(IN1, OUTPUT);
  pinMode(IN2, OUTPUT);
  pinMode(pwmpin, OUTPUT);
  
  Serial.begin(115200);
  startTime = millis()/1000.0;

}

void loop() {
  ref = 0*sin(time*6.28*8);
  computeControlSignal();
  setSpeed(int(controlSignal), IN1, IN2, pwmpin);
  Serial.println(getAngle(myEnc));
  delay(1);


  
  
}

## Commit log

2023-12-09 add scripts for real time visual tracking and communication with arduino over serial
2023-12-19 add folder for cad files
2024-01-04 CAD files
    [Body1_L.SLDPRT, Body1_R.SLDPRT, Body2.SLDPRT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]
2024-01-05 Modified Readme, Arduino live code
2024-07-13 Add script for controlling Odrive with Uno R4 Wifi
2024-09-11 update battery module board; add control boards for head modules
    [BatteryModuleBoard.brd, BatteryModuleBoard.sch, Body1_L.SLDPRT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]
2024-09-11 Update pcb component sizes and power connections
    [BatteryModuleBoard.brd, BatteryModuleBoard.sch, HeadBoard.brd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]
2024-10-18 Generated fabrication files for RoboSoft deadline
    [BatteryModule-BackCover.stl, BatteryModule-Covers.3mf, BatteryModule-FrontCover.3mf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]
2024-10-18 added examples for temp/humidity sensor and IMU on control board
2024-11-20 Update CAD and fab files to RAL fabrication version; add arduino examples for interfacing with components
    [BatteryModule-BackCover.stl, BatteryModule-Covers.3mf, BatteryModule-FrontCover.3mf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]
2024-11-28 add docker services and files for mqtt control; add arduino file for mqtt control
2024-12-04 setup services and arduino code to control fish over MQTT
2024-12-05 Update mqttControl.ino to compute joint angles
2024-12-06 update dualOdriveTest to run both odrives
2024-12-07 fix mqttControl to run ODrives remotely
    [dualODriveTest.ino, mqttControl.ino]
2024-12-11 Add ArUco markers
    [ArUco_4x4_50_ID0.3mf, ArUco_4x4_50_ID0.stl]
2025-02-25 update fab files and create scripts for data processing
    [ArUco_4x4_50_ID1.3mf, ArUco_4x4_50_ID1.stl, ChArUco_Board_4x4_100_40mmSquares.3mf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]
2025-04-23 update fab files; create notebook for processing data
    [FrameCover_ExternalFrame_v217.stl, FrameCovers_FrameCoverOnly.3mf, HeadBottom.3mf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]

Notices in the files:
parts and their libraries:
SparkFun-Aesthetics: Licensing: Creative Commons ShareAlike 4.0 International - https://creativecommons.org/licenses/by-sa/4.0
